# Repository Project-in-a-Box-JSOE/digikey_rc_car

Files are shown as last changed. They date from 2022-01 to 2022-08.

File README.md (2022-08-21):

# SYWMI_RC_Car

**A Digikey collaborated project**
> Project documentation [@Maker.io](https://www.digikey.com/en/maker/profiles/b3c9555ffd7248bcb833dc392372bf2a)<br />
> More about [Project in a Box](https://pibucsd.org/)

## Overview
Create your own remote controlled (RC) car from scratch with Project in a Box (PiB)! This project is jammed packed with ECE concepts, such as communications, hardware and electronic prototyping, CAD, and programming.

## BOM
For simplicity, we will split the project's BOM into three:
- Remote
- Car (Electronics)
- Car (Hardware)

Find them [here](BOM.pdf)

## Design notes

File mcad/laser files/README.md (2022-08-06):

## Laser-cut List
| Part  | Quantity |
| --- | --- |
| Battery Housing Cover (optional)  | 1  |
| Back Housing  | 1  |
| Back Side Housing  | 2  |
| Chassis  | 1  |
| Chassis Front Side Connector  | 2  |
| Chassis Top Front Plate  | 1  |
| Servo Mount  | 1  |
| Remote Bottom Plate  | 1  |

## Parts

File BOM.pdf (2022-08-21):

## REMOTE

PART NAME | PART NUMBER | QUANTITY | URL
Remote PCB | 1 See GitHub for gerber file | **
Arduino Nano | A000005 | | 1 https://www.digikey.com/en/products/detail/arduino/A000005/2638989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
SparkFun Thumbsticks | COM-09032 | | 2 https://www.digikey.com/en/products/detail/sparkfun-electronics/COM-09032/6823623
Female Socket (2x4 pins) | PPPC042LFBN-RC | | 1 https://www.digikey.com/en/products/detail/sullins-connector-solutions/PPPC042LFBN-RC/810244
DC Power Jack Socket | PJ-102AH | | 1 https://www.digikey.com/en/products/detail/cui-devices/PJ-102AH/408448
100nF Ceramic Capacitor | SR205C104KAATR1 | | 1 https://www.digikey.com/en/products/detail/kyocera-avx/SR205C104KAATR1/3660592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
9V Alkaline Battery | 9V-MN1604 | | 1 https://www.digikey.com/en/products/detail/duracell-industrial-operations-inc/9V-MN1604/13280363
Battery Clip w/ DC Power Jack | FIT0043 | | 1 https://www.digikey.com/en/products/detail/dfrobot/FIT0043/7597082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
5mm LED | LTL-4233 | | 1 https://www.digikey.com/en/products/detail/lite-on-inc/LTL-4233/217580
330-ohm Resistor | MFR-25FBF52-330R | | 1 https://www.digikey.com/en/products/detail/yageo/MFR-25FBF52-330R/9138136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
10uF Electrolytic Capacitor | UVR1E100MDD | | 1 https://www.digikey.com/en/products/detail/nichicon/UVR1E100MDD/588798
NRF24L01 Module | NRF24L01 Module | | 1 https://www.amazon.com/Makerfire-Arduino-NRF24L01-Wireless-Transceiver/dp/B00O9O868G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

## Car (Electronics)

PART NAME PART NUMBER QUANTITY URL
Car PCB | 1 See GitHub guide for gerber file | **
Arduino Nano | A000005 | 1 https://www.digikey.com/en/products/detail/arduino/A000005/2638989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
L293D Motor Driver | L293D | 1 https://www.digikey.com/en/products/detail/stmicroelectronics/L293D/634700
100nF Ceramic Capacitor | SR205C104KAATR1 | 2 https://www.digikey.com/en/products/detail/kyocera-avx/SR205C104KAATR1/3660592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
100uF Ceramic Capacitor | TAP107K010SCS | 1 https://www.digikey.com/en/products/detail/kyocera-avx/TAP107K010SCS/563948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
10uF Electrolytic Capacitor | UVR1E100MDD | 2 https://www.digikey.com/en/products/detail/nichicon/UVR1E100MDD/588798
Tactile Button | FSMSMTR | 1 https://www.digikey.com/en/products/detail/te-connectivity-alcoswitch-switches/FSMSMTR/529671
Male Headers | 2011-1X04G00SD025B | 1 https://www.digikey.com/en/products/detail/oupiin-america-inc/2011-1X04G00SD025B/13251799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
8-Pin Right Angle Female Header | PPPC042LJBN-RC | 1 https://www.digikey.com/en/products/detail/sullins-connector-solutions/PPPC042LJBN-RC/776015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
SG90 9g Servo Motor | SER0043 | 1 https://www.digikey.com/en/products/detail/dfrobot/SER0043/7087197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
Small DC Motor | LS-00024 | 1 https://www.digikey.com/en/products/detail/osepp-electronics-ltd/LS-00024/11198647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
NRF24L01 Module | NRF24L01 Module | 1 https://www.amazon.com/Makerfire-Arduino-NRF24L01-Wireless-Transceiver/dp/B00O9O868G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
7.4 LiPo Battery | URGENEX 2S Lipo Battery 7.4v 1100mAh RC Lipo Batteries 8.14Wh 35C Li-Po Battery with Deans T Plug Fit for BEZGAR HS181/HM181, HBX XLH18859E 18859A 16889 16890A, Q903 1/16 Scale RC Car 2 USB Charger 1 https://www.amazon.com/URGENEX-Battery-Rechargeable-Compatibal-Brushless/dp/B08N4RHMNH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

## Car (Hardware)

PART NAME PART NUMBER QUANTITY URL
3D-Printed Parts | 1 See GitHub guide for stl files | **
Laser Cut Chassis | 1 See GitHub guide for laser cut files | **
M2x12mm Socket Head Screw | 91292A834 | 2 https://www.mcmaster.com/91292A835/
M2x8mm Socket Head Screw | 90037A102 | 10 https://www.mcmaster.com/91292A832/
M3x70mm Socket Head Screw | 91290A297 | 1 https://www.mcmaster.com/91290A297/
M3x20mm Socket Head Screw | 90035A138 | 2 https://www.mcmaster.com/91502A109/
M2 Washer | 98689A110 | 2 https://www.mcmaster.com/98689A110/
M3 Washer | 98689A112 | 6 https://www.mcmaster.com/98689A112/
M2 Hex Nut | 90592A004 | 10 https://www.mcmaster.com/90592A004/
M3 Hex Locknut | 93625A100 | 3 https://www.mcmaster.com/93625A100/
Small Shielded Ball Bearings | Small Shielded Ball Bearings | 4 https://www.amazon.com/uxcell-Bearing-Double-Shielded-Bearings/dp/B07FW18RQY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
Tire Grip (sold by four pcs) | MZT302-30 | 1 https://www.kyoshoamerica.com/MZT302-30-LM-Wide-High-Grip-Tire-304pcs_p_4122.html

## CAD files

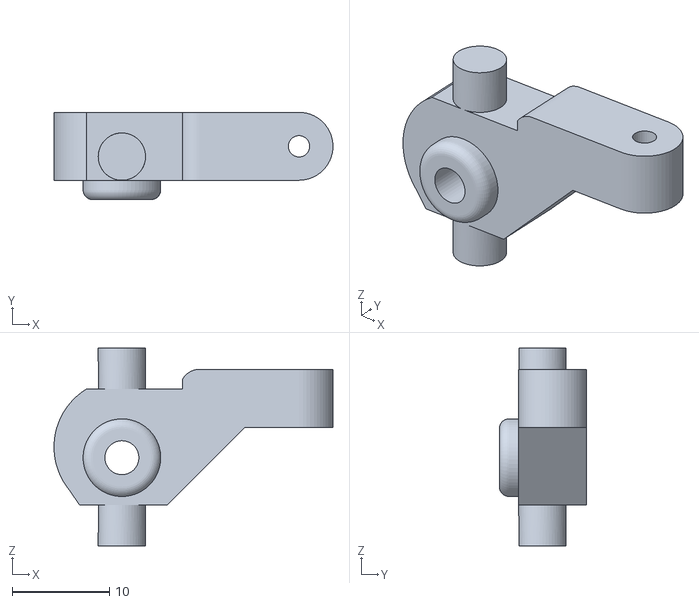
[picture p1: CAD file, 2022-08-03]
mcad/print files/RC_Left_Extended_Front_Axle.stl
28.7 x 9.00 x 20.4

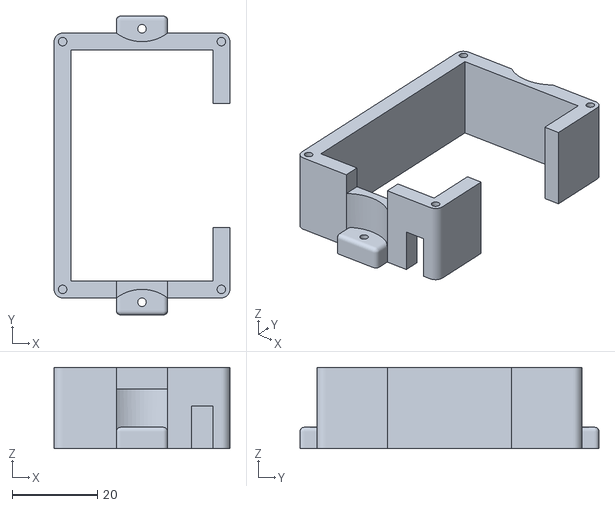
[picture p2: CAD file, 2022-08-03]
mcad/print files/Battery_Housing.stl
41.2 x 70.0 x 19.0

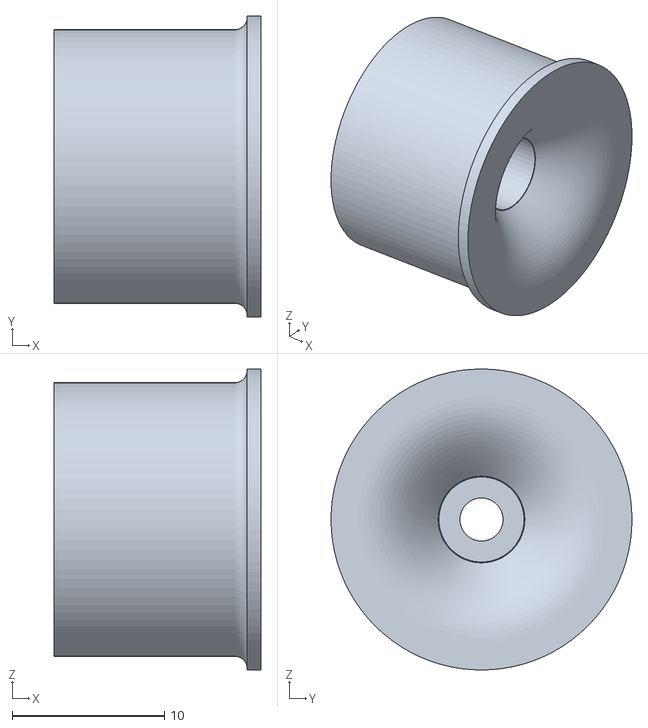
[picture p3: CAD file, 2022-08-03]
mcad/print files/Front_Wheel_Rim.stl
13.6 x 19.8 x 19.8

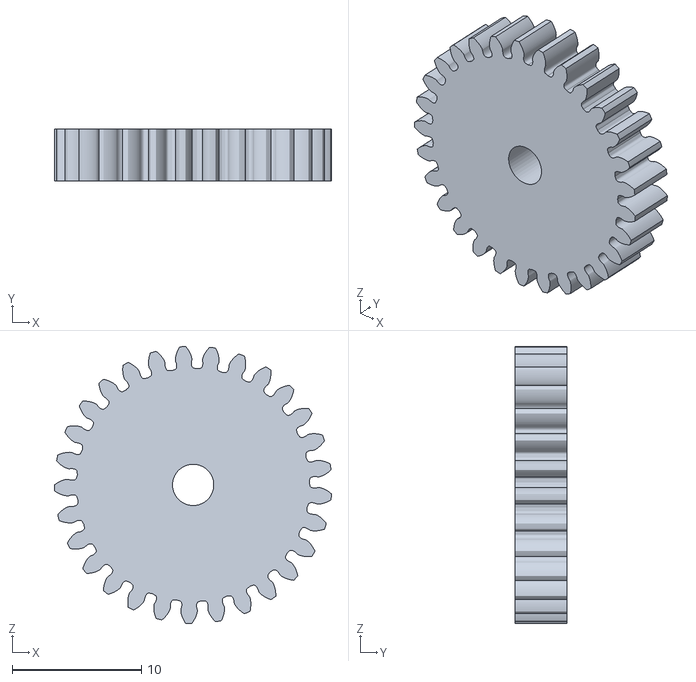
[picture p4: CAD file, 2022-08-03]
mcad/print files/Driver_Gear.stl
21.5 x 4.00 x 21.5

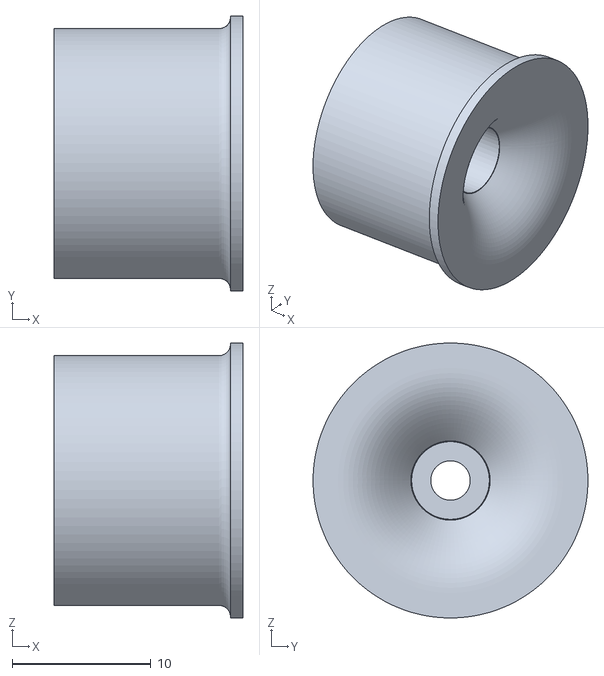
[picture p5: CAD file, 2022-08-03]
mcad/print files/Back_Wheel_Rim.stl
13.6 x 19.8 x 19.8

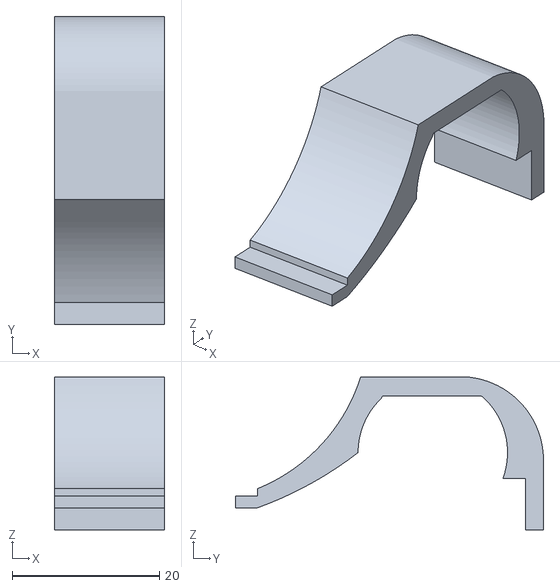
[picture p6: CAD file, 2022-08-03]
mcad/print files/DC_Motor_Mount.stl
15.0 x 41.8 x 20.7

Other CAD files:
mcad/print files/RC_Right_Extended_Front_Axle.stl
mcad/complete_car.f3d
mcad/complete_remote.f3d

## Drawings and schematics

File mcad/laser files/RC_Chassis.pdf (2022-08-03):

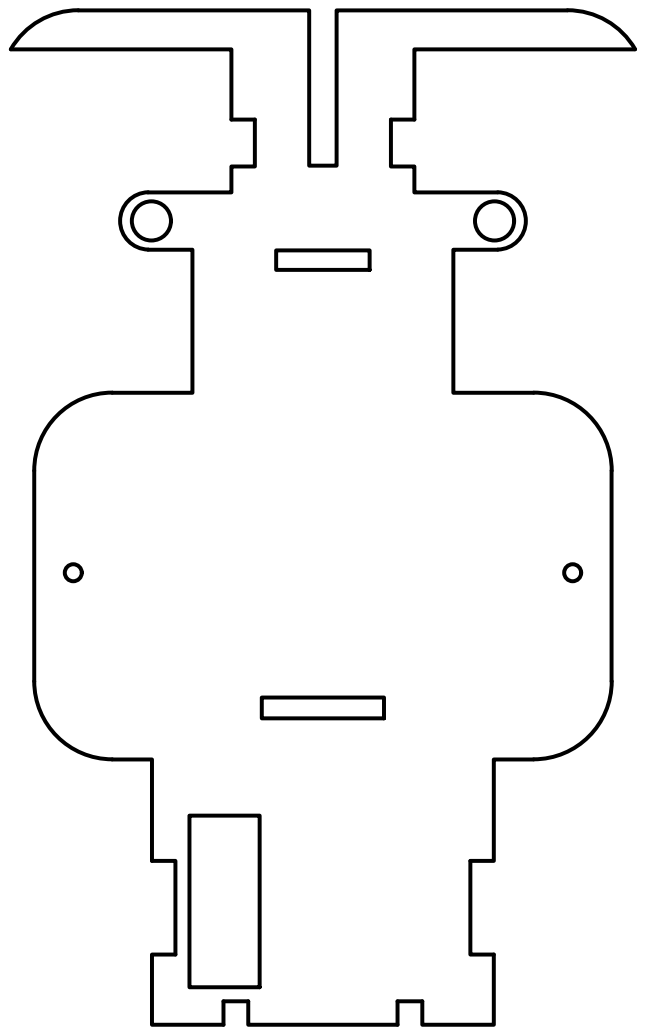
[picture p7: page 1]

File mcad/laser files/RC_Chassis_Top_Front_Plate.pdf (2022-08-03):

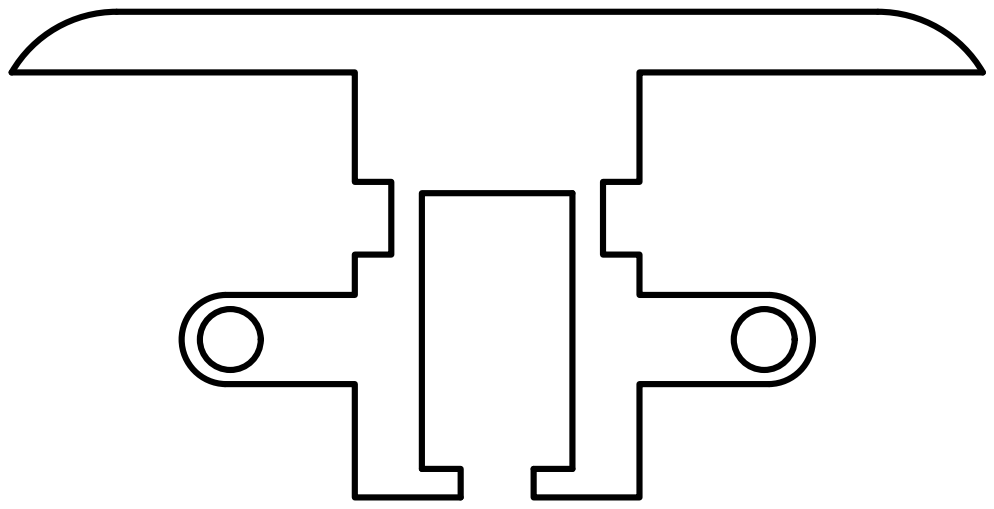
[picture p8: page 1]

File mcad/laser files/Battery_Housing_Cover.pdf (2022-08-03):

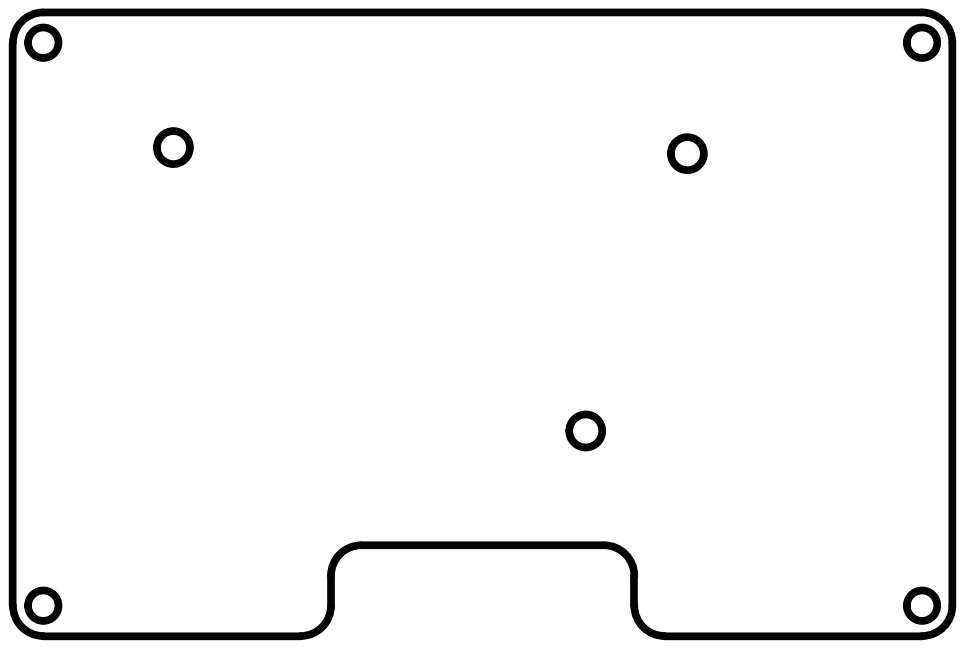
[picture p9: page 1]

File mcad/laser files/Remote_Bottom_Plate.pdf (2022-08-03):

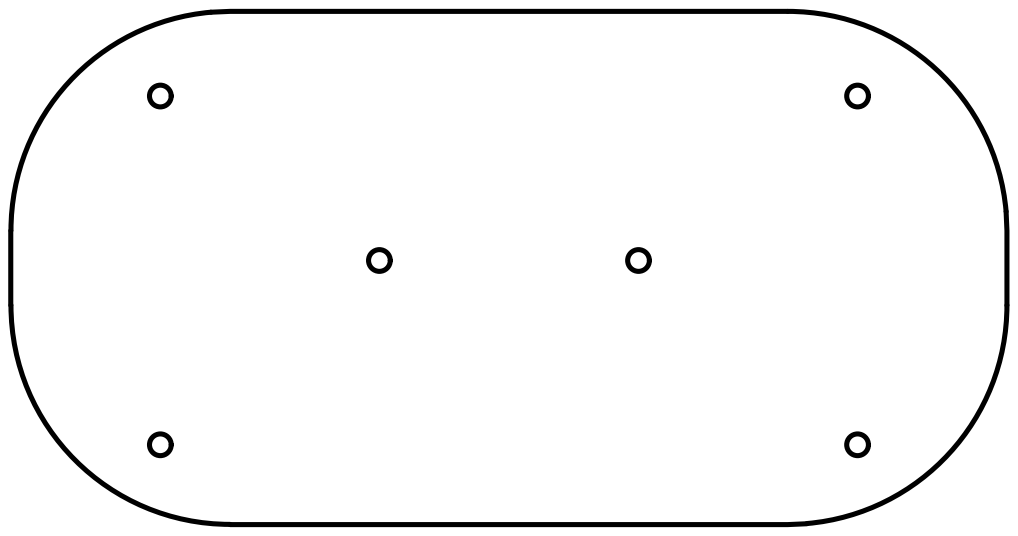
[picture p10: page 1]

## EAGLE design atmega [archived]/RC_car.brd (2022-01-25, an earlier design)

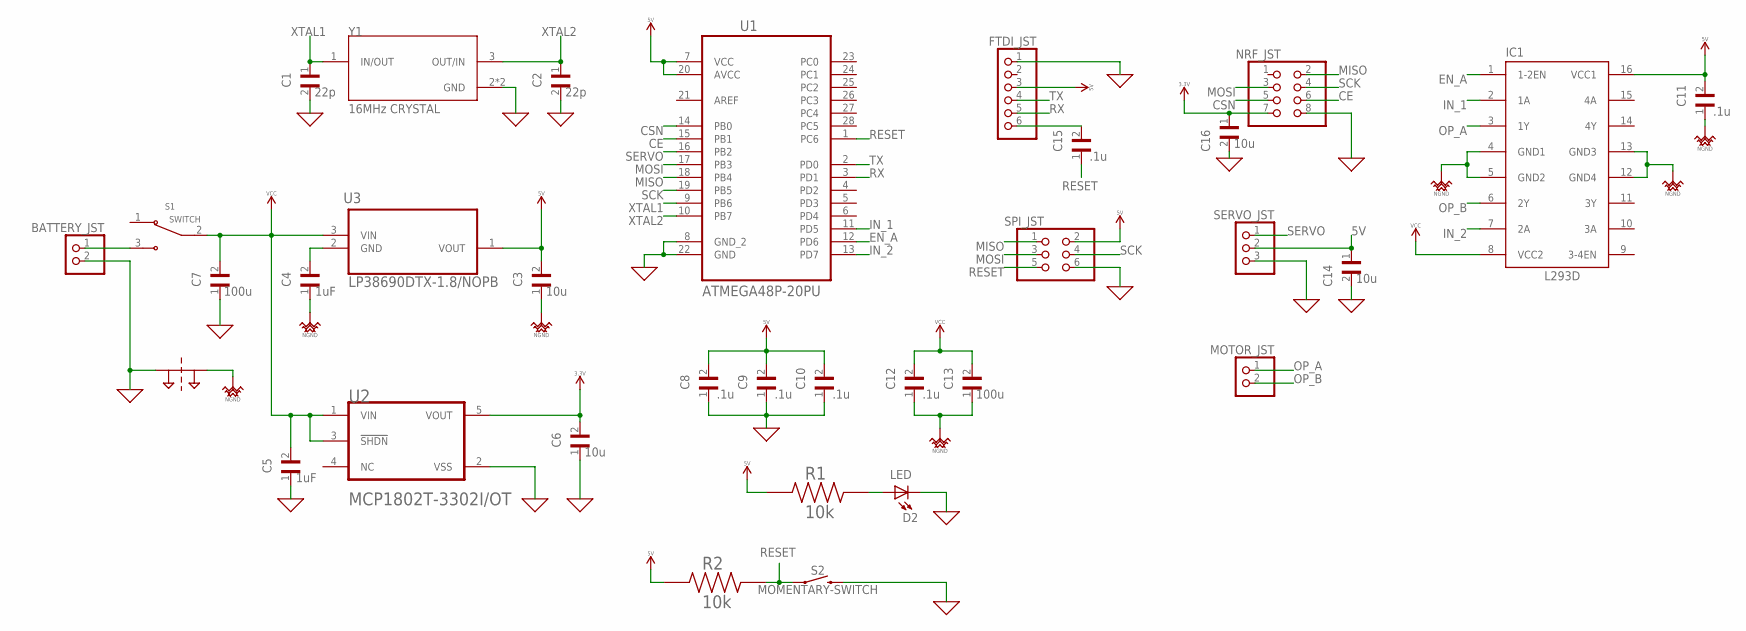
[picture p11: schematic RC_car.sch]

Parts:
BATTERY_JST: PINHD-1X2; 1X02
C1, C2: 22p; CAPC2012X140N
C3, C6: 10u; CAPC2013X95N
C4, C5: 1uF; CAPC2012X70N
C7, C13: 100u; CAPC3225X280N
C8, C9, C10, C11, C12, C15: .1u; CAPC2012X140N
C14, C16: 10u; CAPC1608X90
D2: LED; DIOC200X125X110
FTDI_JST: PINHD-1X6; 1X06
IC1: L293D; DIL16
MOTOR_JST: PINHD-1X2; 1X02
NET_BRIDGE1: NET_BRIDGE
NRF_JST: PINHD-2X4; 2X04
R1, R2: 10k; RESC2012X60N
S1: SWITCH; SW_500SSP1S2M2QEA
S2: MOMENTARY-SWITCH; TACTILE_SWITCH_PTH_6.0MM
SERVO_JST: PINHD-1X3; 1X03
SPI_JST: PINHD-2X3; 2X03
U1: ATMEGA48P-20PU; DIP254P762X457-28
U2: MICROCHIP_MCP1802T-3302I-OTMICROCHIP_MCP1802T-330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; MICROCHIP_MCP1802T-3302I-OT_0
U3: LP38690DTX-1.8/NOPB; TO228P1042X238-3N
Y1: 16MHz CRYSTAL; XTAL_ECS-160-12-33-AGN-TR

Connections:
0: BATTERY_JST.2, C1.2, C2.2, C5.1, C6.1, C7.1, C8.1, C9.1, C10.1, C14.2, C16.2, D2.-, FTDI_JST.1, NET_BRIDGE1.P$1, NRF_JST.8, S2.3 (2), SERVO_JST.3, SPI_JST.6, U1.8 (GND_2), U1.22 (GND), U2.2 (VSS), Y1.2 (GND), Y1.4 (GND)
3.3V: C6.2, C16.1, NRF_JST.7, U2.5 (VOUT)
5V: C3.2, C8.2, C9.2, C10.2, C11.2, C14.1, FTDI_JST.3, IC1.16 (VCC1), R1.1, R2.1, SERVO_JST.2, SPI_JST.2, U1.7 (VCC), U1.20 (AVCC), U3.1 (VOUT)
CE: NRF_JST.6, U1.15 (PB1)
CSN: NRF_JST.5, U1.14 (PB0)
EN_A: IC1.1 (1-2EN), U1.12 (PD6)
IN_1: IC1.2 (1A), U1.11 (PD5)
IN_2: IC1.7 (2A), U1.13 (PD7)
MISO: NRF_JST.2, SPI_JST.1, U1.18 (PB4)
MOSI: NRF_JST.3, SPI_JST.3, U1.17 (PB3)
unnamed: BATTERY_JST.1, S1.3 (NO)
unnamed: C4.2, U3.2 (GND)
unnamed: C15.2, FTDI_JST.6
unnamed: D2.+, R1.2
NGND: C3.1, C4.1, C11.1, C12.1, C13.1, IC1.4 (GND1), IC1.5 (GND2), IC1.12 (GND4), IC1.13 (GND3), NET_BRIDGE1.P$2
OP_A: IC1.3 (1Y), MOTOR_JST.1
OP_B: IC1.6 (2Y), MOTOR_JST.2
RESET: C15.1, R2.2, S2.1, SPI_JST.5, U1.1 (PC6)
RX: FTDI_JST.5, U1.3 (PD1)
SCK: NRF_JST.4, SPI_JST.4, U1.19 (PB5)
SERVO: SERVO_JST.1, U1.16 (PB2)
TX: FTDI_JST.4, U1.2 (PD0)
VCC: C5.2, C7.2, C12.2, C13.2, IC1.8 (VCC2), S1.2 (COM), U2.1 (VIN), U2.3 (!SHDN!), U3.3 (VIN)
XTAL1: C1.1, U1.9 (PB6), Y1.1 (IN/OUT)
XTAL2: C2.1, U1.10 (PB7), Y1.3 (OUT/IN)

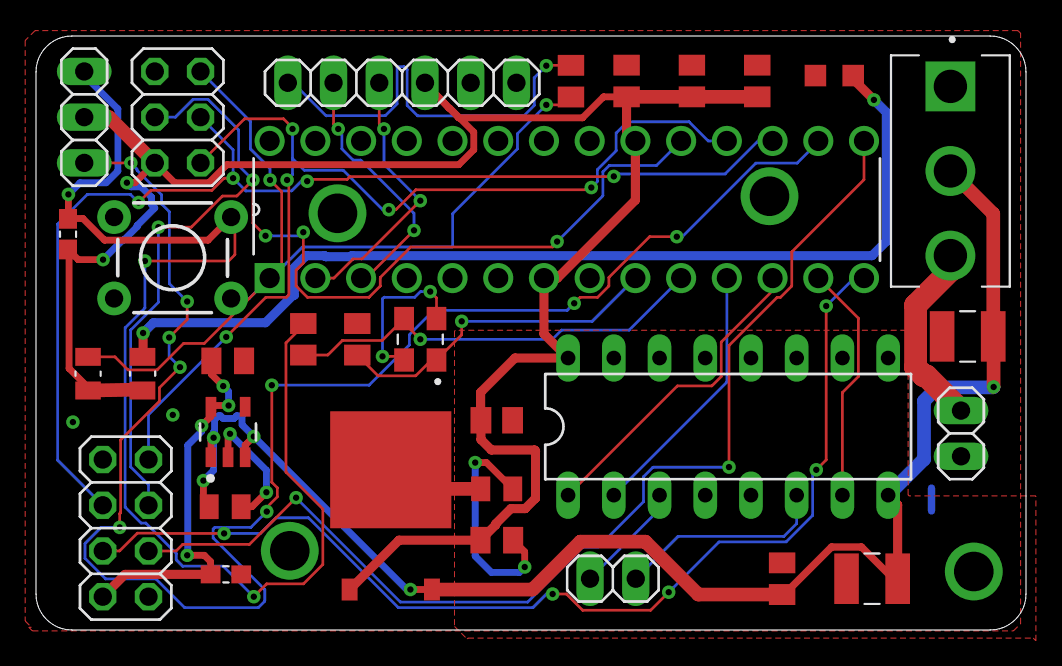
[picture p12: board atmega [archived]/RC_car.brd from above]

Board: 2 copper layers, 55.0 x 33.0 mm, 33 parts (1 on the bottom side), 25 nets.

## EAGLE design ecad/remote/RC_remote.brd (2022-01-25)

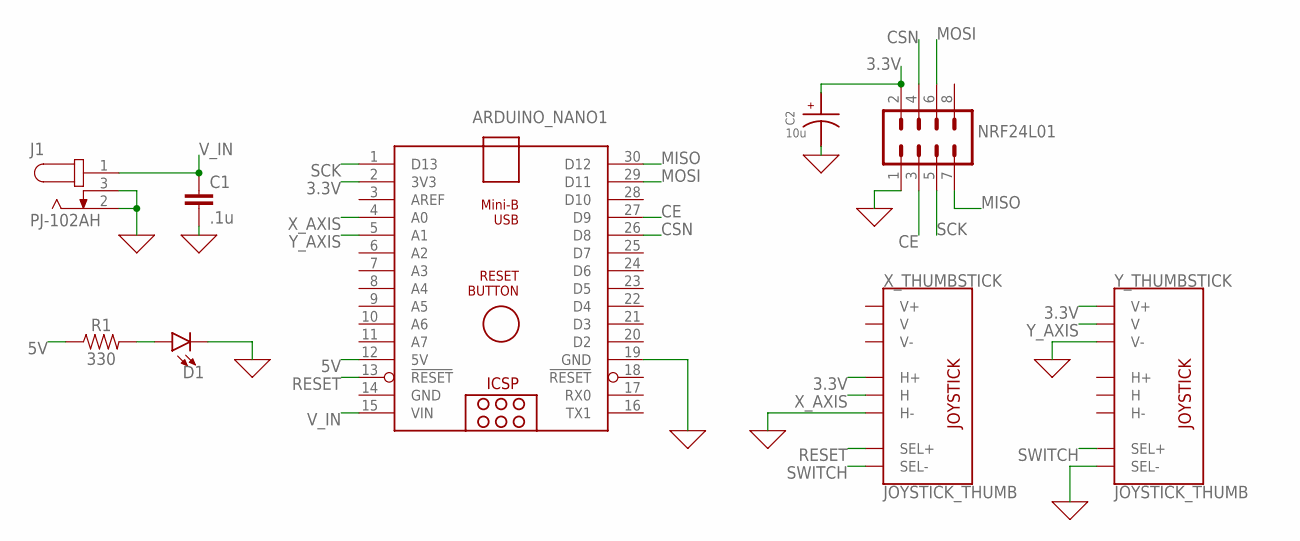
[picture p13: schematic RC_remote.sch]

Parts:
ARDUINO_NANO1: ARDUINO_NANO
C1: .1u; C2.5-3
C2: 10u; CAPPRD200W50D550H1250
D1: LED5MM; LED_5MM
J1: PJ-102AH; CUI_PJ-102AH
NRF24L01: MA04-2
R1: 330; AXIAL-0.3
X_THUMBSTICK: JOYSTICK_THUMB; JOYSTICK
Y_THUMBSTICK: JOYSTICK_THUMB; JOYSTICK

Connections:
0: ARDUINO_NANO1.19 (GND), C1.2, C2.2, D1.K (C), J1.2, J1.3, NRF24L01.1, X_THUMBSTICK.H3 (H-), Y_THUMBSTICK.B2A (SEL-), Y_THUMBSTICK.V3 (V-)
3.3V: ARDUINO_NANO1.2 (3V3), C2.1, NRF24L01.2, X_THUMBSTICK.H1 (H+), Y_THUMBSTICK.V1 (V+)
5V: ARDUINO_NANO1.12 (5V), R1.P$1 (1)
CE: ARDUINO_NANO1.27 (D9), NRF24L01.3
CSN: ARDUINO_NANO1.26 (D8), NRF24L01.4
GND: ARDUINO_NANO1.14 (GND)
MISO: ARDUINO_NANO1.30 (D12), NRF24L01.7
MOSI: ARDUINO_NANO1.29 (D11), NRF24L01.6
unnamed: D1.A, R1.P$2 (2)
RESET: ARDUINO_NANO1.13 (!RESET), X_THUMBSTICK.B1A (SEL+)
SCK: ARDUINO_NANO1.1 (D13), NRF24L01.5
SWITCH: X_THUMBSTICK.B2A (SEL-), Y_THUMBSTICK.B1A (SEL+)
V_IN: ARDUINO_NANO1.15 (VIN), C1.1, J1.1
X_AXIS: ARDUINO_NANO1.4 (A0), X_THUMBSTICK.H2 (H)
Y_AXIS: ARDUINO_NANO1.5 (A1), Y_THUMBSTICK.V2 (V)

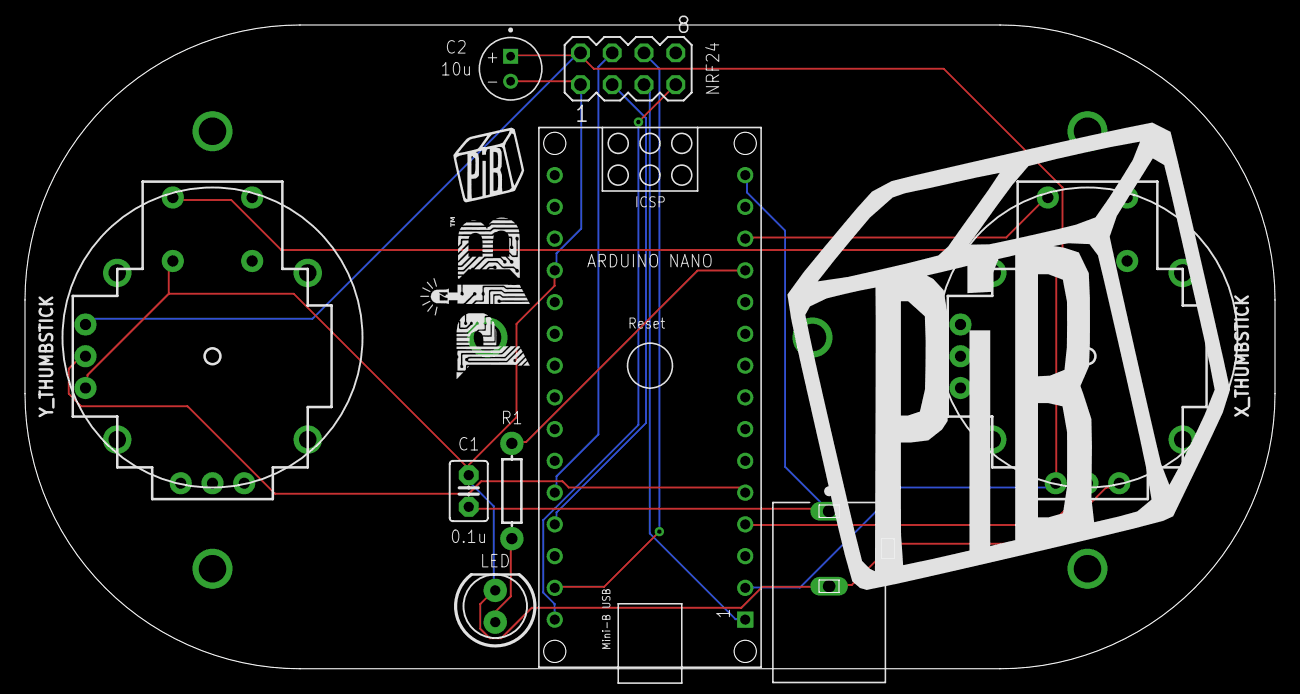
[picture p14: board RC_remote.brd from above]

Board: 2 copper layers, 100.0 x 51.5 mm, 13 parts (1 on the bottom side), 14 nets.

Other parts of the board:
U$1: PIB_LOGO_40MM
U$2: PIB-LOGO
U$3, U$4: PIB_LOGO_10MM

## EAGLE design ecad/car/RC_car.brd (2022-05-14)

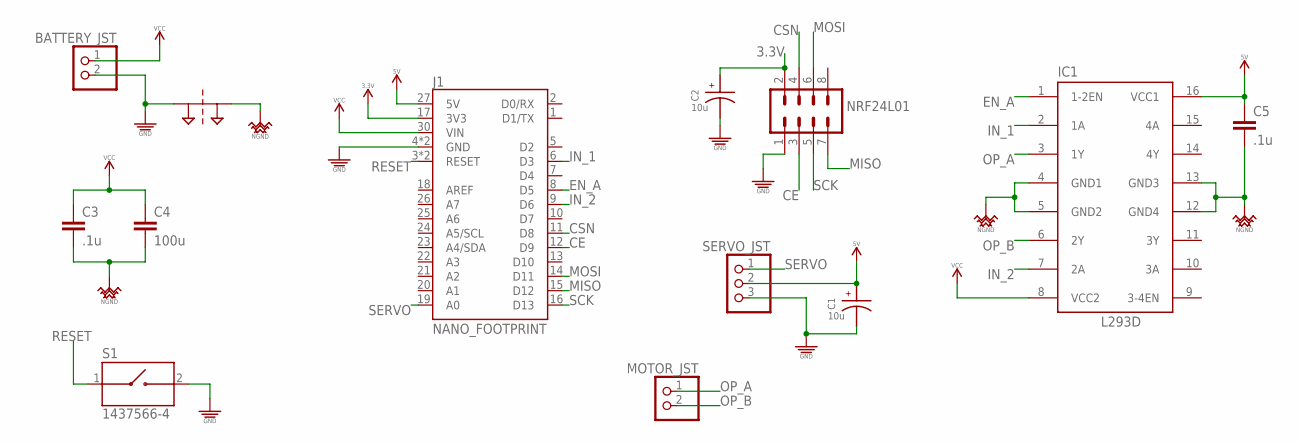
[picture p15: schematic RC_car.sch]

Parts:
BATTERY_JST: PINHD-1X2; 1X02
C1, C2: 10u; CAPPRD200W50D550H1250
C3, C5: .1u; C2.5-3
C4: 100u; C2.5-3
IC1: L293D; DIL16
J1: NANO_FOOTPRINT; NANO
MOTOR_JST: PINHD-1X2; 1X02
NET_BRIDGE1: NET_BRIDGE
NRF24L01: MA04-2
S1: 1437566-4; SW_1437566-4
SERVO_JST: PINHD-1X3; 1X03

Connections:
3.3V: C2.1, J1.17 (3V3), NRF24L01.2
5V: C1.1, C5.1, IC1.16 (VCC1), J1.27 (5V), SERVO_JST.2
CE: J1.12 (D9), NRF24L01.3
CSN: J1.11 (D8), NRF24L01.4
EN_A: IC1.1 (1-2EN), J1.8 (D5)
GND: BATTERY_JST.2, C1.2, C2.2, J1.4 (GND), J1.29 (GND), NET_BRIDGE1.P$1, NRF24L01.1, S1.2, SERVO_JST.3
IN_1: IC1.2 (1A), J1.6 (D3)
IN_2: IC1.7 (2A), J1.9 (D6)
MISO: J1.15 (D12), NRF24L01.7
MOSI: J1.14 (D11), NRF24L01.6
NGND: C3.2, C4.2, C5.2, IC1.4 (GND1), IC1.5 (GND2), IC1.12 (GND4), IC1.13 (GND3), NET_BRIDGE1.P$2
OP_A: IC1.3 (1Y), MOTOR_JST.1
OP_B: IC1.6 (2Y), MOTOR_JST.2
RESET: J1.3 (RESET), J1.28 (RESET), S1.1
SCK: J1.16 (D13), NRF24L01.5
SERVO: J1.19 (A0), SERVO_JST.1
VCC: BATTERY_JST.1, C3.1, C4.1, IC1.8 (VCC2), J1.30 (VIN)

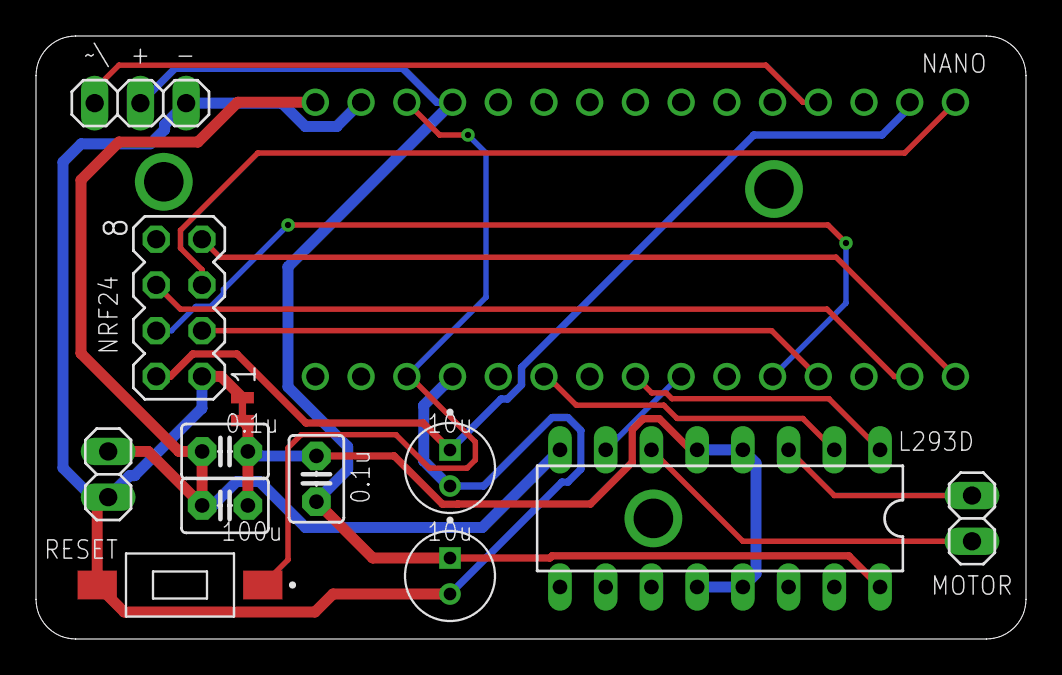
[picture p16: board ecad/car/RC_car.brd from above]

Board: 2 copper layers, 55.0 x 33.5 mm, 13 parts (0 on the bottom side), 17 nets.

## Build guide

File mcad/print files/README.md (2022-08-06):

## Print List
| Part  | Quantity |
| --- | --- |
| Back Wheel Rim  | 2  |
| Battery Housing  | 1  |
| DC Motor Mount  | 1  |
| Driver Gear  | 1  |
| Front Wheel Rim  | 2  |
| Left Extended Front Axle  | 1  |
| Right Extended Front Axle  | 1  |

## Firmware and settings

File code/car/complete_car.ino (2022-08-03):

//Include Libraries
#include <SPI.h>
#include <nRF24L01.h>
#include <RF24.h>
#include <Servo.h>

#define BAUDRATE 9600
#define CE 9
#define CSN 8

// Motor pinout
#define enA 5
#define in1 6
#define in2 10

// Servo pinout
#define servo_pin A0

// Create an RF24 object
RF24 radio(CE, CSN);

// Create servo object
Servo servo;

// Unique address through which two modules communicate.
const byte address[6] = "00001";

int raw_analog_reading_x, raw_analog_reading_y;

void setup() {

  Serial.begin(BAUDRATE);

  radio.begin();
  
  //set the address
  radio.openReadingPipe(0, address);
  
  //Set module as receiver
  radio.startListening();

  // Set all the motor control pins to outputs
  pinMode(enA, OUTPUT);
  pinMode(in1, OUTPUT);
  pinMode(in2, OUTPUT);

  // Attach servo pin to Servo object
  servo.attach(servo_pin);
  
  // Turn off motors - Initial state
  digitalWrite(in1, LOW);
  digitalWrite(in2, LOW);
  
}

// Receives the x and y inputs from the remote
void receive_thumbstick_inputs() {

  int inputs[2];

  // Read the data if available in buffer
  if(radio.available()) {
    radio.read(&inputs, sizeof(inputs));
  }

  // Refresh current joystick input readings
  raw_analog_reading_x = inputs[0];
  raw_analog_reading_y = inputs[1];
  
}

// Maps current reading of x thumbstick to servo arm
void map_servo() {

  // Tweak joystick min and max mapped values as necessary
  int servo_pos = map(raw_analog_reading_x, 0, 686, 0, 180);
  
  servo.write(servo_pos);
  
}

// Maps current reading of y thumbstick to motor
void map_motomoto() {

  int motor_speed = 100;  // Feel free to tweak. For PWM maximum possible values are 0 to 255

  if(raw_analog_reading_y > 500){
    // Forward. Tweak threshold to +5 of middle/rest state analog reading
    digitalWrite(in1, HIGH);
    digitalWrite(in1, HIGH);
    digitalWrite(in2, LOW);
  }
  else if(raw_analog_reading_y < 50){
    // Backward. Tweak threshold to -5 of middle/rest state analog reading
    digitalWrite(in1, LOW);
    digitalWrite(in2, HIGH);
  }
  else { 
    // Stop
    digitalWrite(in1, LOW);
    digitalWrite(in2, LOW);
  }
  
  analogWrite(enA, motor_speed);
  
}

void loop() {

  receive_thumbstick_inputs();
  
  map_servo();

  map_motomoto();

  Serial.print("(X,Y)=(");
  Serial.print(raw_analog_reading_x);
  Serial.print(",");
  Serial.print(raw_analog_reading_y);
  Serial.println(")");
 
}

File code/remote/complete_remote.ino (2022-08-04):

//Include Libraries
#include <SPI.h>
#include <nRF24L01.h>
#include <RF24.h>

#define BAUDRATE 9600
#define CE 9
#define CSN 8

// Pinout for two thumbsticks
#define thumbstick_x A0
#define thumbstick_y A1

// Create an RF24 object
RF24 radio(CE, CSN);

// Unique address through which two modules communicate.
const byte address[6] = "00001";

int raw_analog_reading_x, raw_analog_reading_y;

void setup() {

  Serial.begin(BAUDRATE);

  radio.begin();

  //set the address
  radio.openWritingPipe(address);

  //Set module as transmitter
  radio.stopListening();

}

// Sends the x and y inputs to the car
void send_joystick_inputs() {

  const int inputs[2] = {raw_analog_reading_x, raw_analog_reading_y};

  radio.write(&inputs, sizeof(inputs));

  delay(10);

}

void loop() {

  Serial.print("(X,Y)=");

  Serial.print("(");

  // Read + print thumbstick X
  raw_analog_reading_x = analogRead(thumbstick_x);
  Serial.print(raw_analog_reading_x);

  Serial.print(",");

  // Read + print thumbstick Y
  raw_analog_reading_y = analogRead(thumbstick_y);
  Serial.print(raw_analog_reading_y);

  Serial.println(")");

  send_joystick_inputs();

}

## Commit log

2021-12-22 motor driver example update
2021-12-23 motor driver and servo integ example
2021-12-23 compeleted schematic
2022-01-25 v1 eagle files
    [RC_car.brd, RC_car.sch, RC_remote.brd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]
2022-02-23 laser cut files
2022-04-29 print files
    [DC_Motor_Mount.stl, Driver_Gear.stl, Motor_Gear.stl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]
2022-05-14 nano rc car
    [RC_car.brd, RC_car.sch]
2022-05-14 pcb step model
    [RC_car.brd, RC_car.step]
2022-05-15 flipped header
    [untitled.brd]
2022-08-03 remove outdated files
    [DC_Motor_Mount.stl, Driver_Gear.stl, Motor_Gear.stl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]
2022-08-03 ecad cleanup
    [RC_car.brd, RC_car.sch, RC_remote.brd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]
2022-08-03 updated mcad files
    [Back_Wheel_Rim.stl, Battery_Housing.stl, DC_Motor_Mount.stl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]
2022-08-21 static bom link
2022-08-23 atmega design
    [RC_car.brd, RC_car.sch]

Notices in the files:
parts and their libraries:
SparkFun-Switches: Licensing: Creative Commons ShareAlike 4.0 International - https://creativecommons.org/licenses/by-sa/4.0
